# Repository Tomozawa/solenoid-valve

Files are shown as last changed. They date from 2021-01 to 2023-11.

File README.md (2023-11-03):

# solenoid-valve
[こちら](https://github.com/funi007/solenoid-valve.git)の電磁弁基板の改良版です。未テストですので使用に際しては十分注意してください。

# 履歴
## 改良基板の初版
- 2023/11/03
- ERC and DRC check
- 6f543627d558cafed8350256de44e78604443efa
- 改良基板の初期版。未テスト。

# 改良点
## フォトリレーが焼ける問題を解消
フォトリレーに負電圧がかかることで内部のFETが焼ける問題を解消しました。フォトリレー自体を採用せず、FETによるオープンドレイン出力としました。

## XT30コネクタに変更
駆動用電源のコネクタをEPコネクタからXT30コネクタ(オス)に変更しました。

## DCDCコンバータの安定性・効率を向上
DCDCコンバータに適正な負荷をかけ、連続モードでの動作とすることで、DCDCコンバータの安定性を改善ました。また、効率の上昇や高調波ノイズの低減も期待できます。

## フォトカプラへの配線を改善
ベタパターンの島ができにくいように、フォトカプラへの配線をまとめました。

# 問題点

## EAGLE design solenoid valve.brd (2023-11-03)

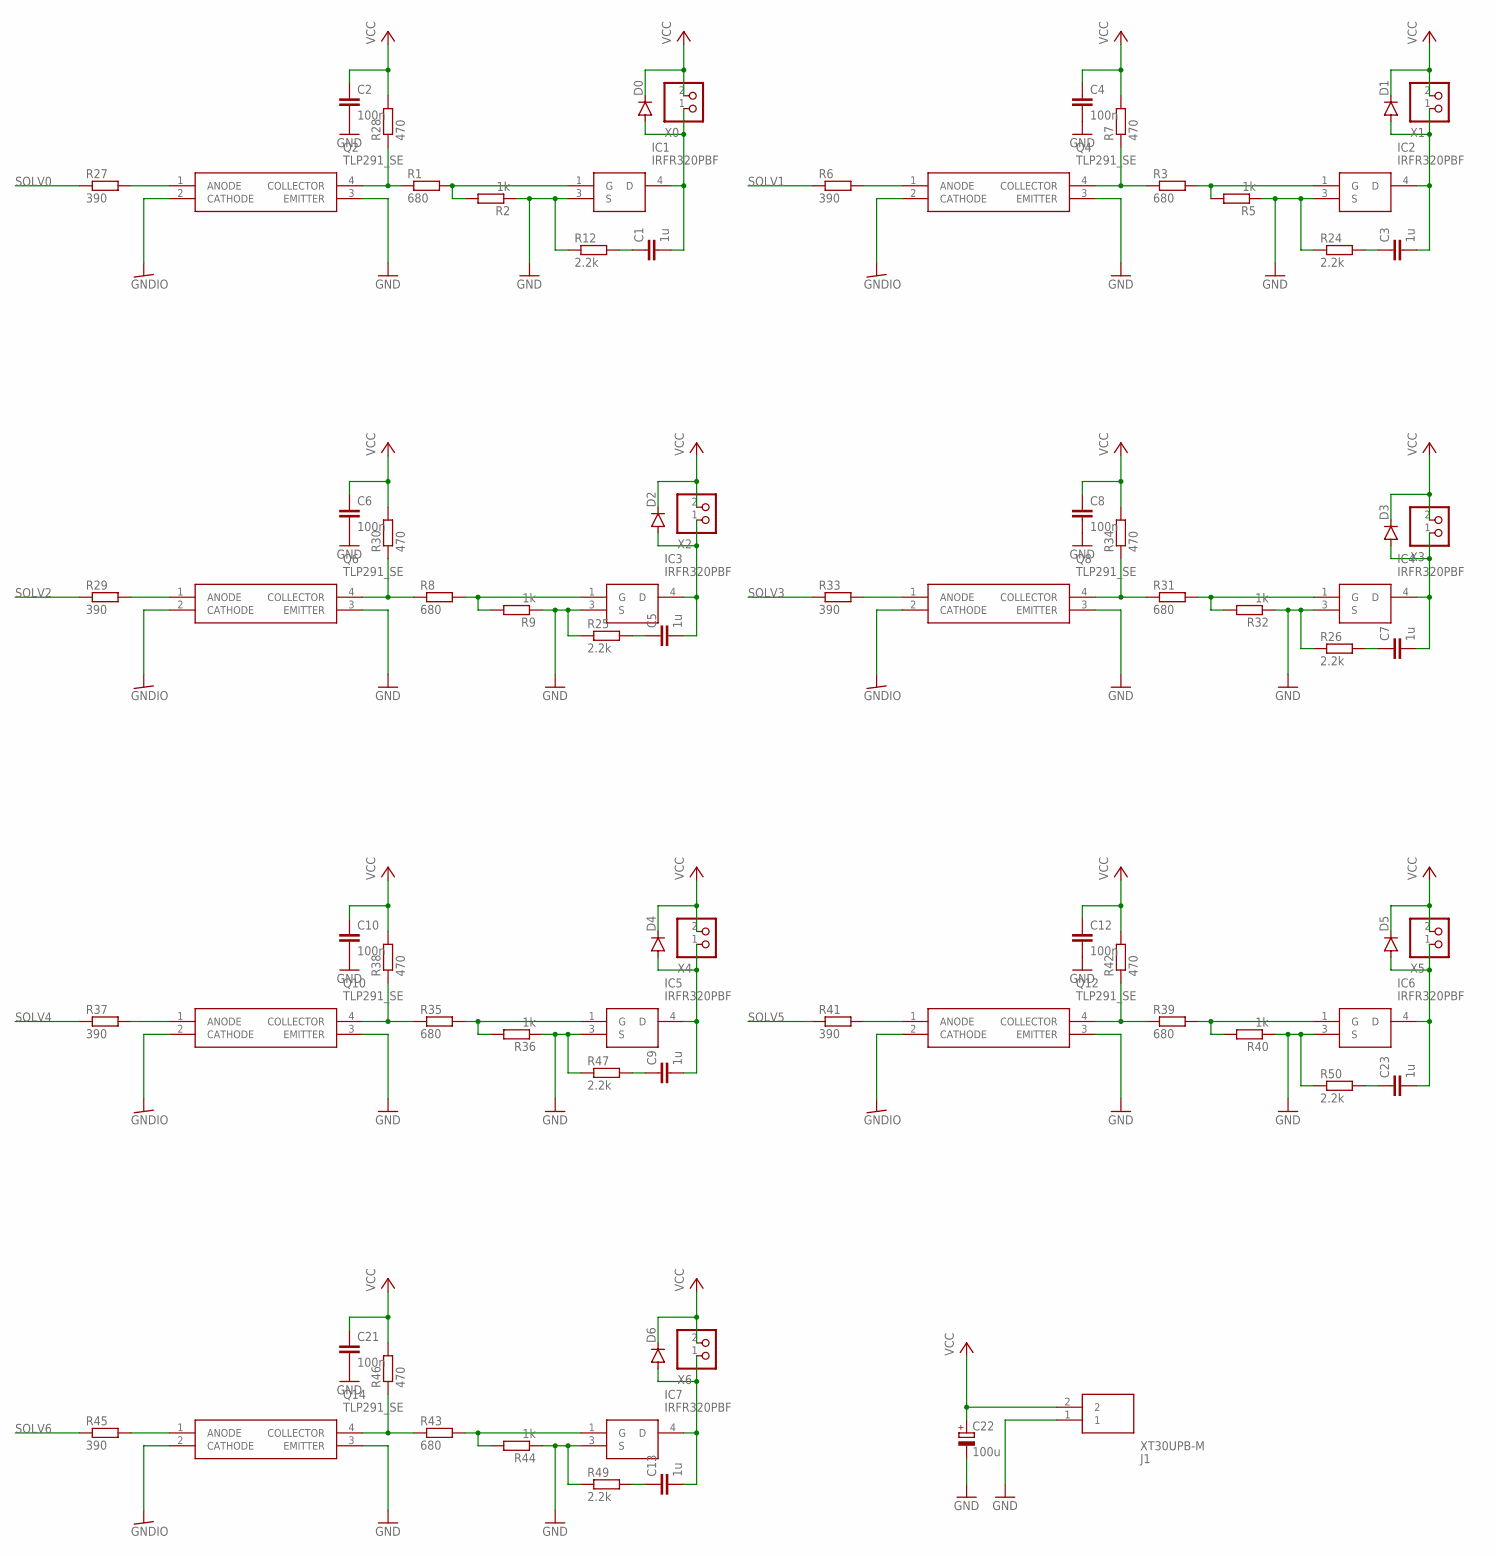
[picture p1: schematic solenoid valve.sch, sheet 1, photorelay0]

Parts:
C1, C3, C5, C7, C9, C13, C23: 1u; C0603
C2, C4, C6, C8, C10, C12, C21: 100n; C0603
C22: 100u; E2-5
D0, D1, D2, D3, D4, D5, D6: DIODE-SOD123; SOD123
IC1, IC2, IC3, IC4, IC5, IC6, IC7: IRFR320PBF; TO228P990X238-3N
J1: XT30UPB-M; SHDR2W160P0X500_1X2_1020X520X1
Q2, Q4, Q6, Q8, Q10, Q12, Q14: TLP291_SE; SOIC127P700X230-4N
R1, R3, R8, R31, R35, R39, R43: 680; R0603
R2, R5, R9, R32, R36, R40, R44: 1k; R0603
R6, R27, R29, R33, R37, R41, R45: 390; R0603
R7, R28, R30, R34, R38, R42, R46: 470; R0603
R12, R24, R25, R26, R47, R49, R50: 2.2k; R0603
X0, X1, X2, X3, X4, X5, X6: S2B-XASK-1

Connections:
GND: C2.2, C4.2, C6.2, C8.2, C10.2, C12.2, C21.2, C22.-, IC1.3 (S), IC2.3 (S), IC3.3 (S), IC4.3 (S), IC5.3 (S), IC6.3 (S), IC7.3 (S), J1.1, Q2.3 (EMITTER), Q4.3 (EMITTER), Q6.3 (EMITTER), Q8.3 (EMITTER), Q10.3 (EMITTER), Q12.3 (EMITTER), Q14.3 (EMITTER), R2.1, R5.1, R9.1, R12.1, R24.1, R25.1, R26.1, R32.1, R36.1, R40.1, R44.1, R47.1, R49.1, R50.1
GNDIO: Q2.2 (CATHODE), Q4.2 (CATHODE), Q6.2 (CATHODE), Q8.2 (CATHODE), Q10.2 (CATHODE), Q12.2 (CATHODE), Q14.2 (CATHODE); also elsewhere on the board
unnamed: IC2.1 (G), R3.2, R5.2
unnamed: C3.2, D1.A, IC2.4 (D), X1.1
unnamed: Q2.4 (COLLECTOR), R1.1, R28.1
unnamed: Q4.1 (ANODE), R6.2
unnamed: Q4.4 (COLLECTOR), R3.1, R7.1
unnamed: IC1.1 (G), R1.2, R2.2
unnamed: C1.2, D0.A, IC1.4 (D), X0.1
unnamed: IC3.1 (G), R8.2, R9.2
unnamed: Q2.1 (ANODE), R27.2
unnamed: C5.2, D2.A, IC3.4 (D), X2.1
unnamed: Q6.1 (ANODE), R29.2
unnamed: Q6.4 (COLLECTOR), R8.1, R30.1
unnamed: C7.2, D3.A, IC4.4 (D), X3.1
unnamed: C9.2, D4.A, IC5.4 (D), X4.1
unnamed: IC4.1 (G), R31.2, R32.2
unnamed: C3.1, R24.2
unnamed: C23.1, R50.2
unnamed: C23.2, D5.A, IC6.4 (D), X5.1
unnamed: C5.1, R25.2
unnamed: IC7.1 (G), R43.2, R44.2
unnamed: Q8.1 (ANODE), R33.2
unnamed: Q8.4 (COLLECTOR), R31.1, R34.1
unnamed: IC5.1 (G), R35.2, R36.2
unnamed: Q10.1 (ANODE), R37.2
unnamed: Q10.4 (COLLECTOR), R35.1, R38.1
unnamed: IC6.1 (G), R39.2, R40.2
unnamed: Q12.1 (ANODE), R41.2
unnamed: Q12.4 (COLLECTOR), R39.1, R42.1
unnamed: C13.2, D6.A, IC7.4 (D), X6.1
unnamed: Q14.1 (ANODE), R45.2
unnamed: Q14.4 (COLLECTOR), R43.1, R46.1
unnamed: C7.1, R26.2
unnamed: C9.1, R47.2
unnamed: C13.1, R49.2
unnamed: C1.1, R12.2
SOLV0: R27.1; also elsewhere on the board
SOLV1: R6.1; also elsewhere on the board
SOLV2: R29.1; also elsewhere on the board
SOLV3: R33.1; also elsewhere on the board
SOLV4: R37.1; also elsewhere on the board
SOLV5: R41.1; also elsewhere on the board
SOLV6: R45.1; also elsewhere on the board
VCC: C2.1, C4.1, C6.1, C8.1, C10.1, C12.1, C21.1, C22.+, D0.C, D1.C, D2.C, D3.C, D4.C, D5.C, D6.C, J1.2, R7.2, R28.2, R30.2, R34.2, R38.2, R42.2, R46.2, X0.2, X1.2, X2.2, X3.2, X4.2, X5.2, X6.2

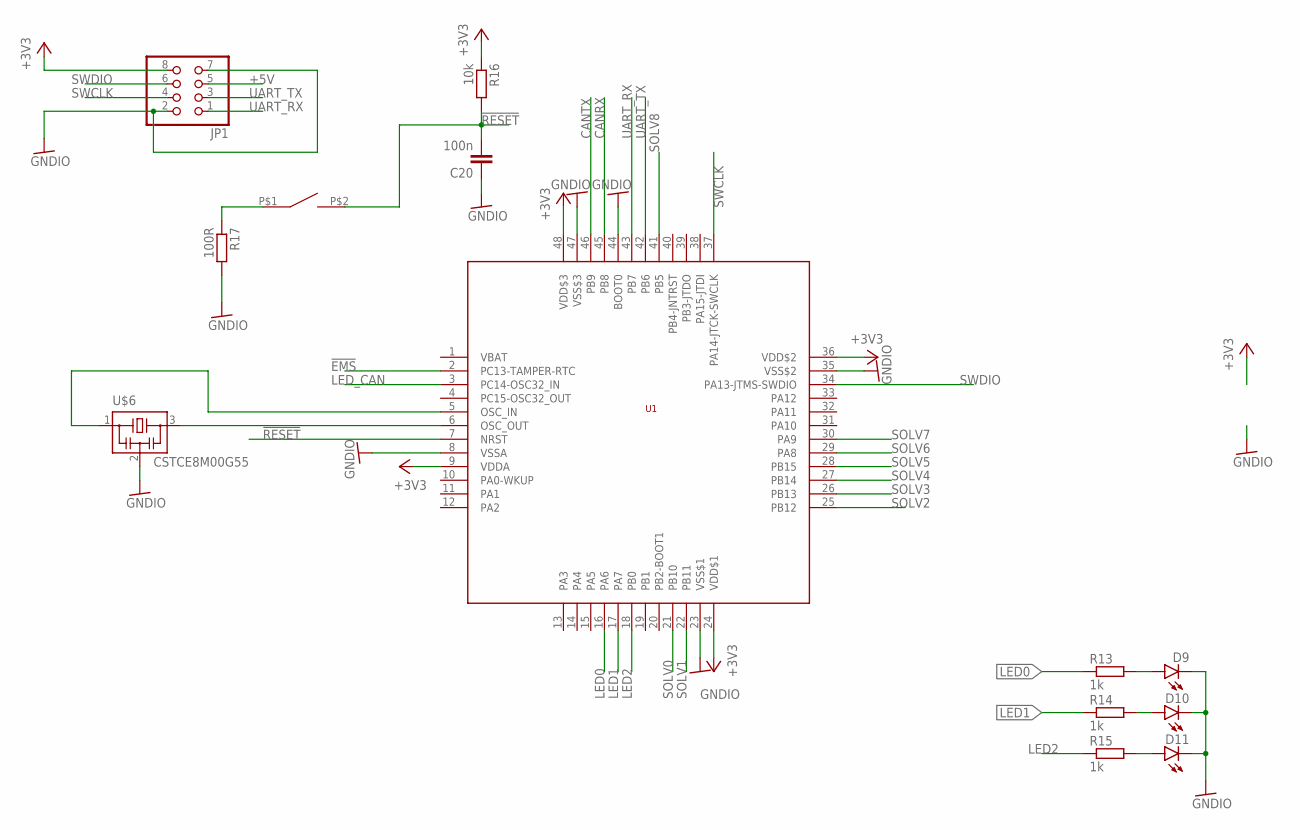
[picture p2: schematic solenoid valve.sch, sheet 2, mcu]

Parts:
C20: 100n; C0603
D9, D10, D11: LEDCHIPLED_0805; CHIPLED_0805
JP1: PINHD-2X4; 2X04
R13, R14, R15: 1k; R0603
R16: 10k; R0603
R17: 100R; R0603
SW1: SWITCH_TACTILETOP; SWITCH_TACTILE_3X6
U1: STM32F103C8; LQFP48
U$6: CSTCE8M00G55

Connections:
!EMS: U1.2 (PC13-TAMPER-RTC); also elsewhere on the board
!RESET: C20.2, R16.2, SW1.P$2 (2), U1.7 (NRST)
+3V3: JP1.8, R16.1, U1.9 (VDDA), U1.24 (VDD$1), U1.36 (VDD$2), U1.48 (VDD$3); also elsewhere on the board
+5V: JP1.5; also elsewhere on the board
CANRX: U1.45 (PB8); also elsewhere on the board
CANTX: U1.46 (PB9); also elsewhere on the board
GNDIO: C20.1, D9.C, D10.C, D11.C, JP1.2, JP1.7, R17.2, U1.8 (VSSA), U1.23 (VSS$1), U1.35 (VSS$2), U1.44 (BOOT0), U1.47 (VSS$3), U$6.2; also elsewhere on the board
LED0: R13.1, U1.16 (PA6)
LED1: R14.1, U1.17 (PA7)
LED2: R15.1, U1.18 (PB0)
LED_CAN: U1.3 (PC14-OSC32_IN); also elsewhere on the board
unnamed: D10.A, R14.2
unnamed: D9.A, R13.2
unnamed: U1.6 (OSC_OUT), U$6.3
unnamed: R17.1, SW1.P$1 (1)
unnamed: U1.5 (OSC_IN), U$6.1
unnamed: D11.A, R15.2
SOLV0: U1.21 (PB10); also elsewhere on the board
SOLV1: U1.22 (PB11); also elsewhere on the board
SOLV2: U1.25 (PB12); also elsewhere on the board
SOLV3: U1.26 (PB13); also elsewhere on the board
SOLV4: U1.27 (PB14); also elsewhere on the board
SOLV5: U1.28 (PB15); also elsewhere on the board
SOLV6: U1.29 (PA8); also elsewhere on the board
SOLV7: U1.30 (PA9)
SOLV8: U1.41 (PB5)
SWCLK: JP1.4, U1.37 (PA14-JTCK-SWCLK)
SWDIO: JP1.6, U1.34 (PA13-JTMS-SWDIO)
UART_RX: JP1.1, U1.43 (PB7)
UART_TX: JP1.3, U1.42 (PB6)

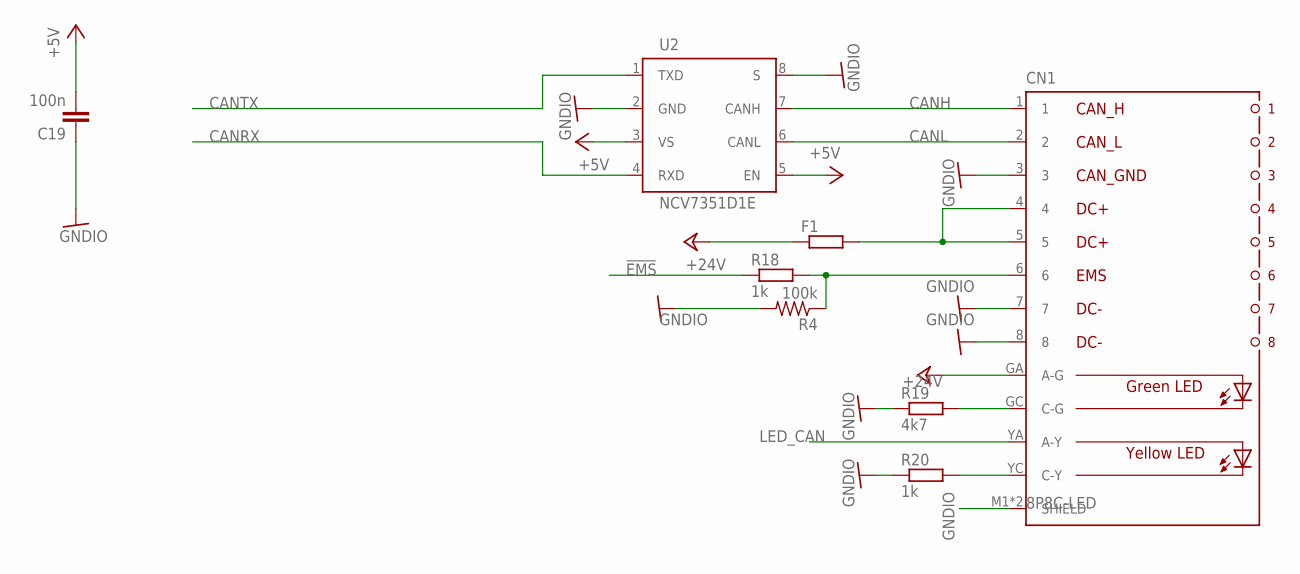
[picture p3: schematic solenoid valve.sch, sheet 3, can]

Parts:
C19: 100n; C0603
CN1: 8P8C-LED
F1: R-EU_R1206; R1206
R4: 100k; R0603
R18, R20: 1k; R0603
R19: 4k7; R0603
U2: NCV7351D1E; SO08

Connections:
!EMS: R18.1; also elsewhere on the board
+5V: C19.2, U2.3 (VS), U2.5 (EN); also elsewhere on the board
+24V: CN1.GA (A-G), F1.1; also elsewhere on the board
CANH: CN1.1, U2.7 (CANH)
CANL: CN1.2, U2.6 (CANL)
CANRX: U2.4 (RXD); also elsewhere on the board
CANTX: U2.1 (TXD); also elsewhere on the board
GNDIO: C19.1, CN1.3, CN1.7, CN1.8, CN1.M1 (SHIELD), CN1.M2 (SHIELD), R4.2, R19.1, R20.1, U2.2 (GND), U2.8 (S); also elsewhere on the board
LED_CAN: CN1.YA (A-Y); also elsewhere on the board
unnamed: CN1.4, CN1.5, F1.2
unnamed: CN1.YC (C-Y), R20.2
unnamed: CN1.GC (C-G), R19.2
unnamed: CN1.6, R4.1, R18.2

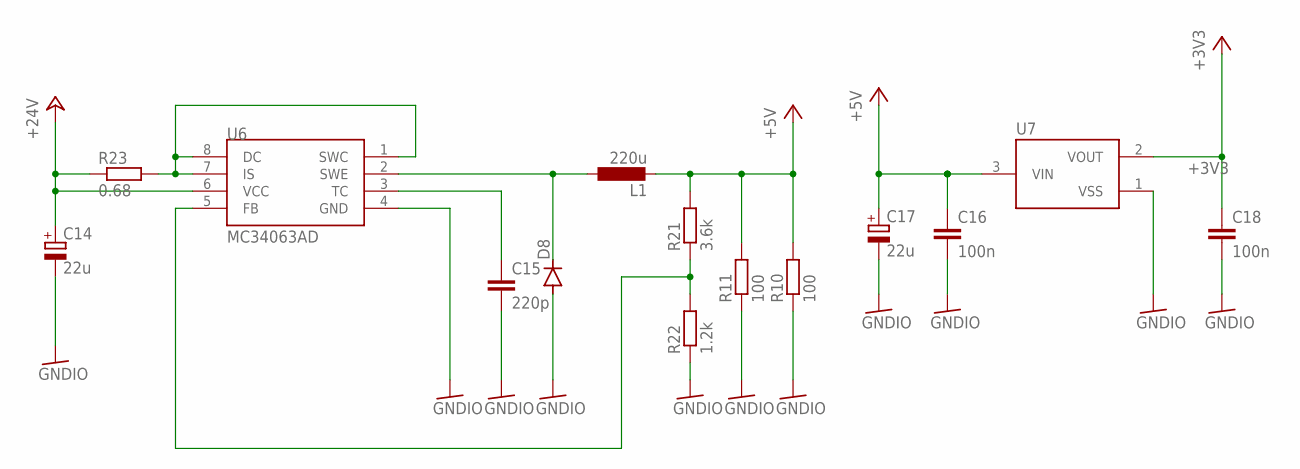
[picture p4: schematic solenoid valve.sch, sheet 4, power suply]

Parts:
C14, C17: 22u; E2-5
C15: 220p; C0603
C16, C18: 100n; C0603
D8: DIODE-SOD123; SOD123
L1: 220u; L5852
R10, R11: 100; R0603
R21: 3.6k; R0603
R22: 1.2k; R0603
R23: 0.68; R1206
U6: MC34063AD; SOIC8
U7: XC6206; SOT95P240X110-3

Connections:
+3V3: C18.1, U7.2 (VOUT); also elsewhere on the board
+5V: C16.1, C17.+, L1.P$2 (2), R10.2, R11.2, R21.2, U7.3 (VIN); also elsewhere on the board
+24V: C14.+, R23.1, U6.6 (VCC); also elsewhere on the board
GNDIO: C14.-, C15.2, C16.2, C17.-, C18.2, D8.A, R10.1, R11.1, R22.1, U6.4 (GND), U7.1 (VSS); also elsewhere on the board
unnamed: R23.2, U6.1 (SWC), U6.7 (IS), U6.8 (DC)
unnamed: D8.C, L1.P$1 (1), U6.2 (SWE)
unnamed: C15.1, U6.3 (TC)
unnamed: R21.1, R22.2, U6.5 (FB)

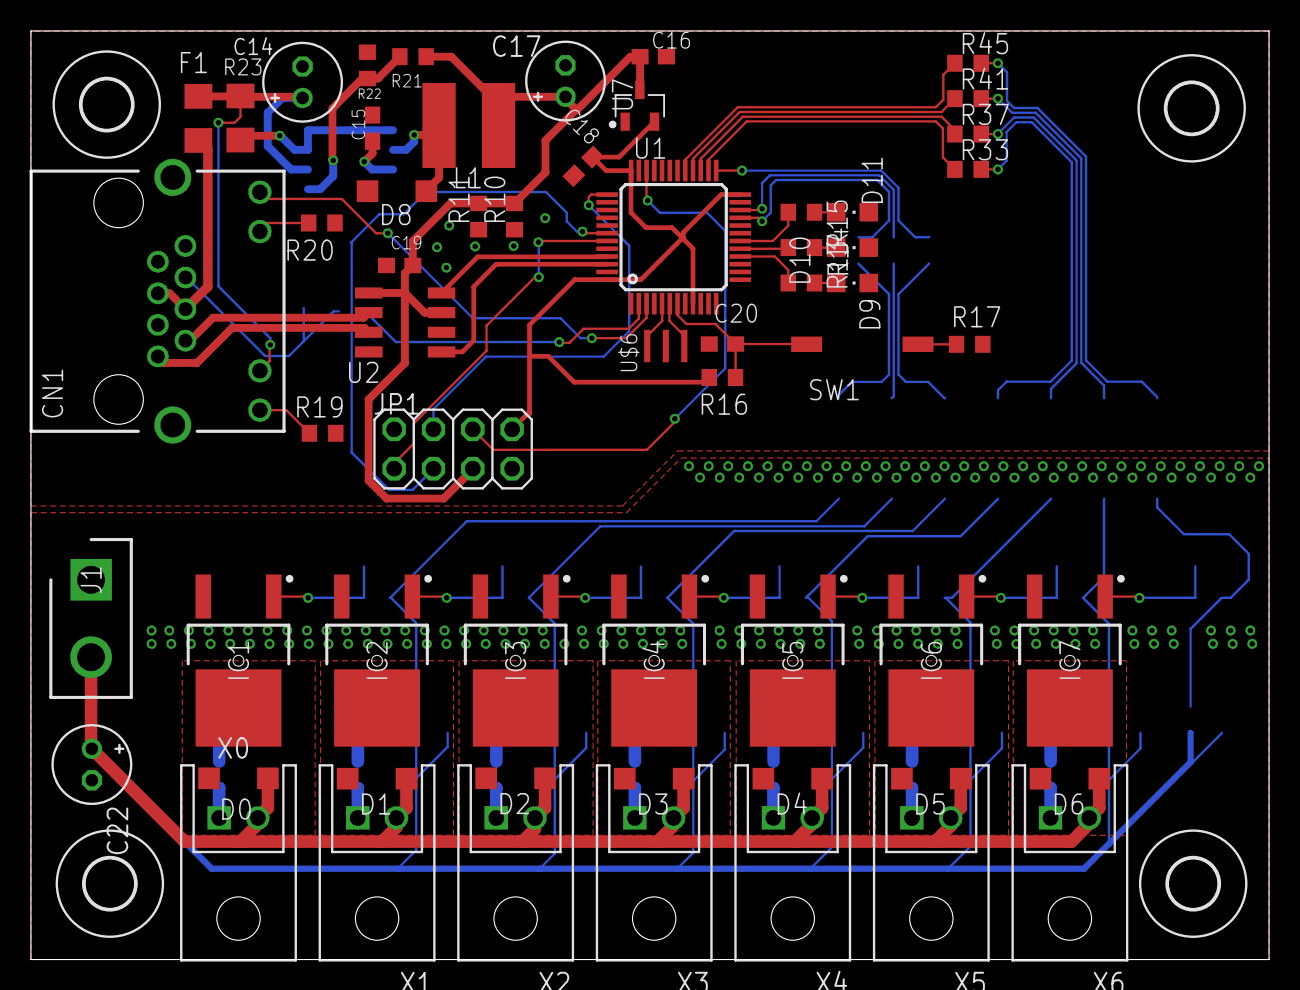
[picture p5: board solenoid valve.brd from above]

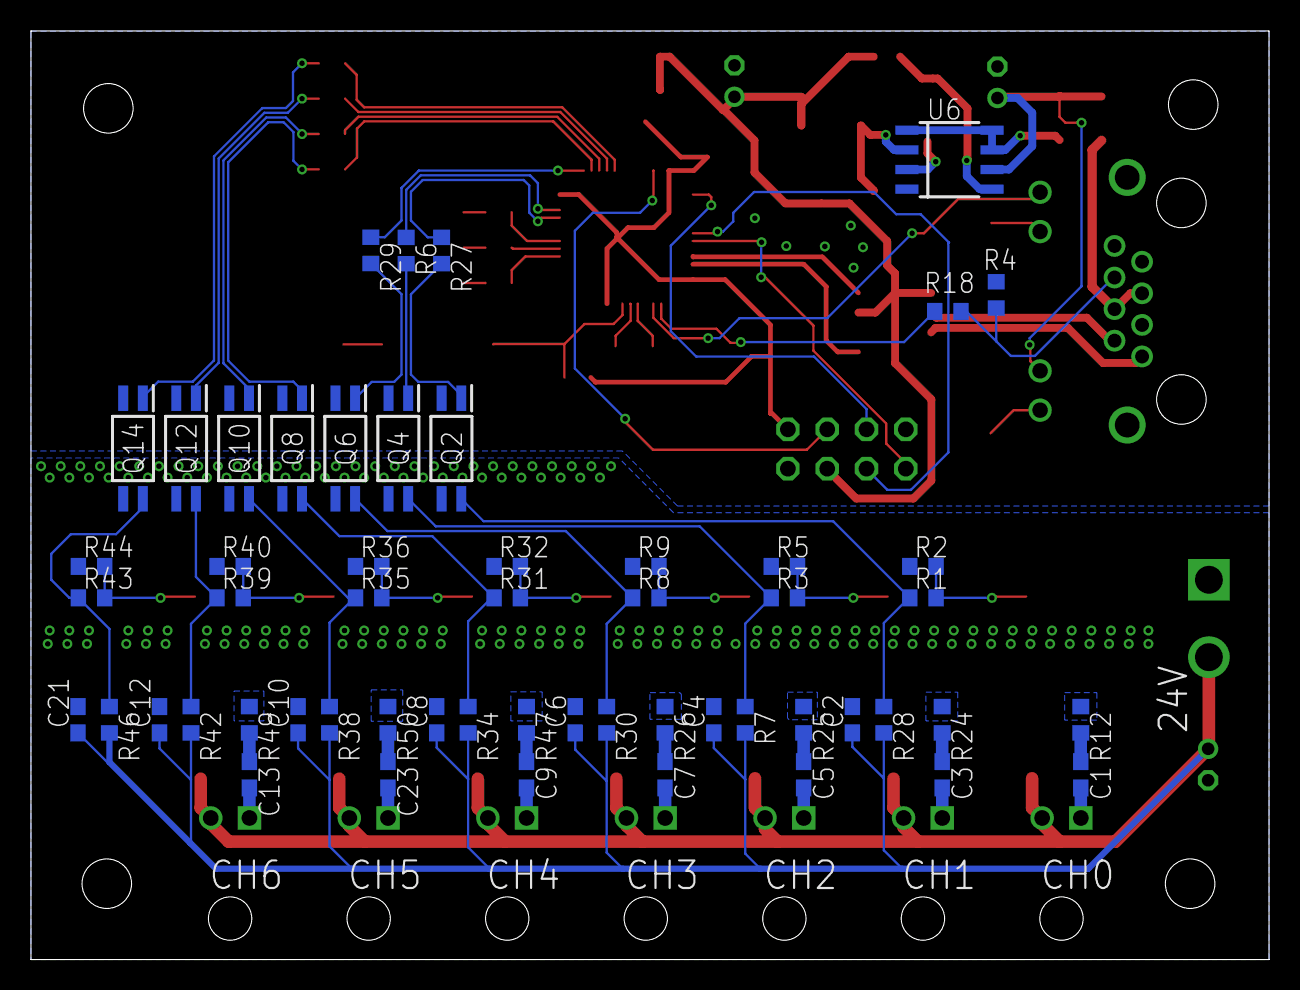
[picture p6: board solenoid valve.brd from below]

Board: 2 copper layers, 80.0 x 60.0 mm, 118 parts (55 on the bottom side), 76 nets.

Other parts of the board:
U$1, U$2, U$3, U$4: 3,2

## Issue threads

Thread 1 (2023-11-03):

フォトカプラの配線について

YUKICHI6105, 2023-11-03:
フォトカプラの配線の隙間にGNDを通さないのはおそらく悪手です。べたGNDを入れるのは内部外部のノイズを低減することにあるので配線間にべたGNDを入れるのが筋です。CANのような近づけた方が効果のあるものならくっつけるべきですが、この場合はノイズが入ると致命的なので間にべたGNDを入れるべきでしょう。

じゃ、頑張れ。あと今日来なかった恨みはいつか晴らす

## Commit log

2023-11-03 Anti Reverse Voltage
2023-11-03 ERC and DRC check
    [solenoid valve.brd, solenoid valve.sch]
